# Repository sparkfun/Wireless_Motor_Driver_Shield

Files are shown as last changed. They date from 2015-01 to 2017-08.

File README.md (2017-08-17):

SparkFun Wireless Motor Driver Shield
=====================================

SparkFun Wireless Motor Driver Shield

[*SparkFun Wireless Motor Driver Shield (DEV-14285)*](https://www.sparkfun.com/products/14285)
Arduino shield with built-in motor driver and XBee slot.

This is an Arduino shield that integrates an H-Bridge Driver and breaks out 
all I/O ports to three-pin headers on a GND / PWR / SIG standard. This enables quick
prototyping and integration of Arduino projects without the need of a breadboard.

This board contains an XBee header for adding wireless capability to your Arduino projects. A switch for 
SW_Serial ties the TX/RX lines to pins A0 and A1 on the Arduino board. 

This shield is a perfect addition to building up a simiple robotics platform with an
Arduino board. Two switches allow you to select which power source is used to power the motors and/or servos.
See [the hookup guide](https://learn.sparkfun.com/tutorials/wireless-motor-driver-shield-hookup-guide#hardware-overview) for a chart showing the various switch configurations.

**Note:** If connected to your Arduino, the switch must be set to SW_Serial in order to program your board. 

Repository Contents
-------------------

* **/Firmware** - Example code 
* **/Hardware** - Eagle design files (.brd, .sch)
* **/Production** - Production panel files (.brd)

Documentation
--------------
* **[Hookup Guide](https://learn.sparkfun.com/tutorials/wireless-motor-driver-shield-hookup-guide)** - Basic hookup guide for the Wireless Motor Driver Shield.
* **[SparkFun Fritzing repo](https://github.com/sparkfun/Fritzing_Parts)** - Fritzing diagrams for SparkFun products.
* **[SparkFun 3D Model repo](https://github.com/sparkfun/3D_Models)** - 3D models of SparkFun products. 

Version History
---------------
* [vH14](https://github.com/sparkfun/Ludus_ProtoShield_Wireless/tree/vH14) - Current version
* [vH11](https://github.com/sparkfun/Ludus_ProtoShield_Wireless/tree/V_1.1) - The product formerly known as the Ludus ProtoShield Wireless

License Information
-------------------

This product is _**open source**_! 

Please review the LICENSE.md file for license information. 

If you have any questions or concerns on licensing, please contact techsupport@sparkfun.com.

Distributed as-is; no warranty is given.

- Your friends at SparkFun.

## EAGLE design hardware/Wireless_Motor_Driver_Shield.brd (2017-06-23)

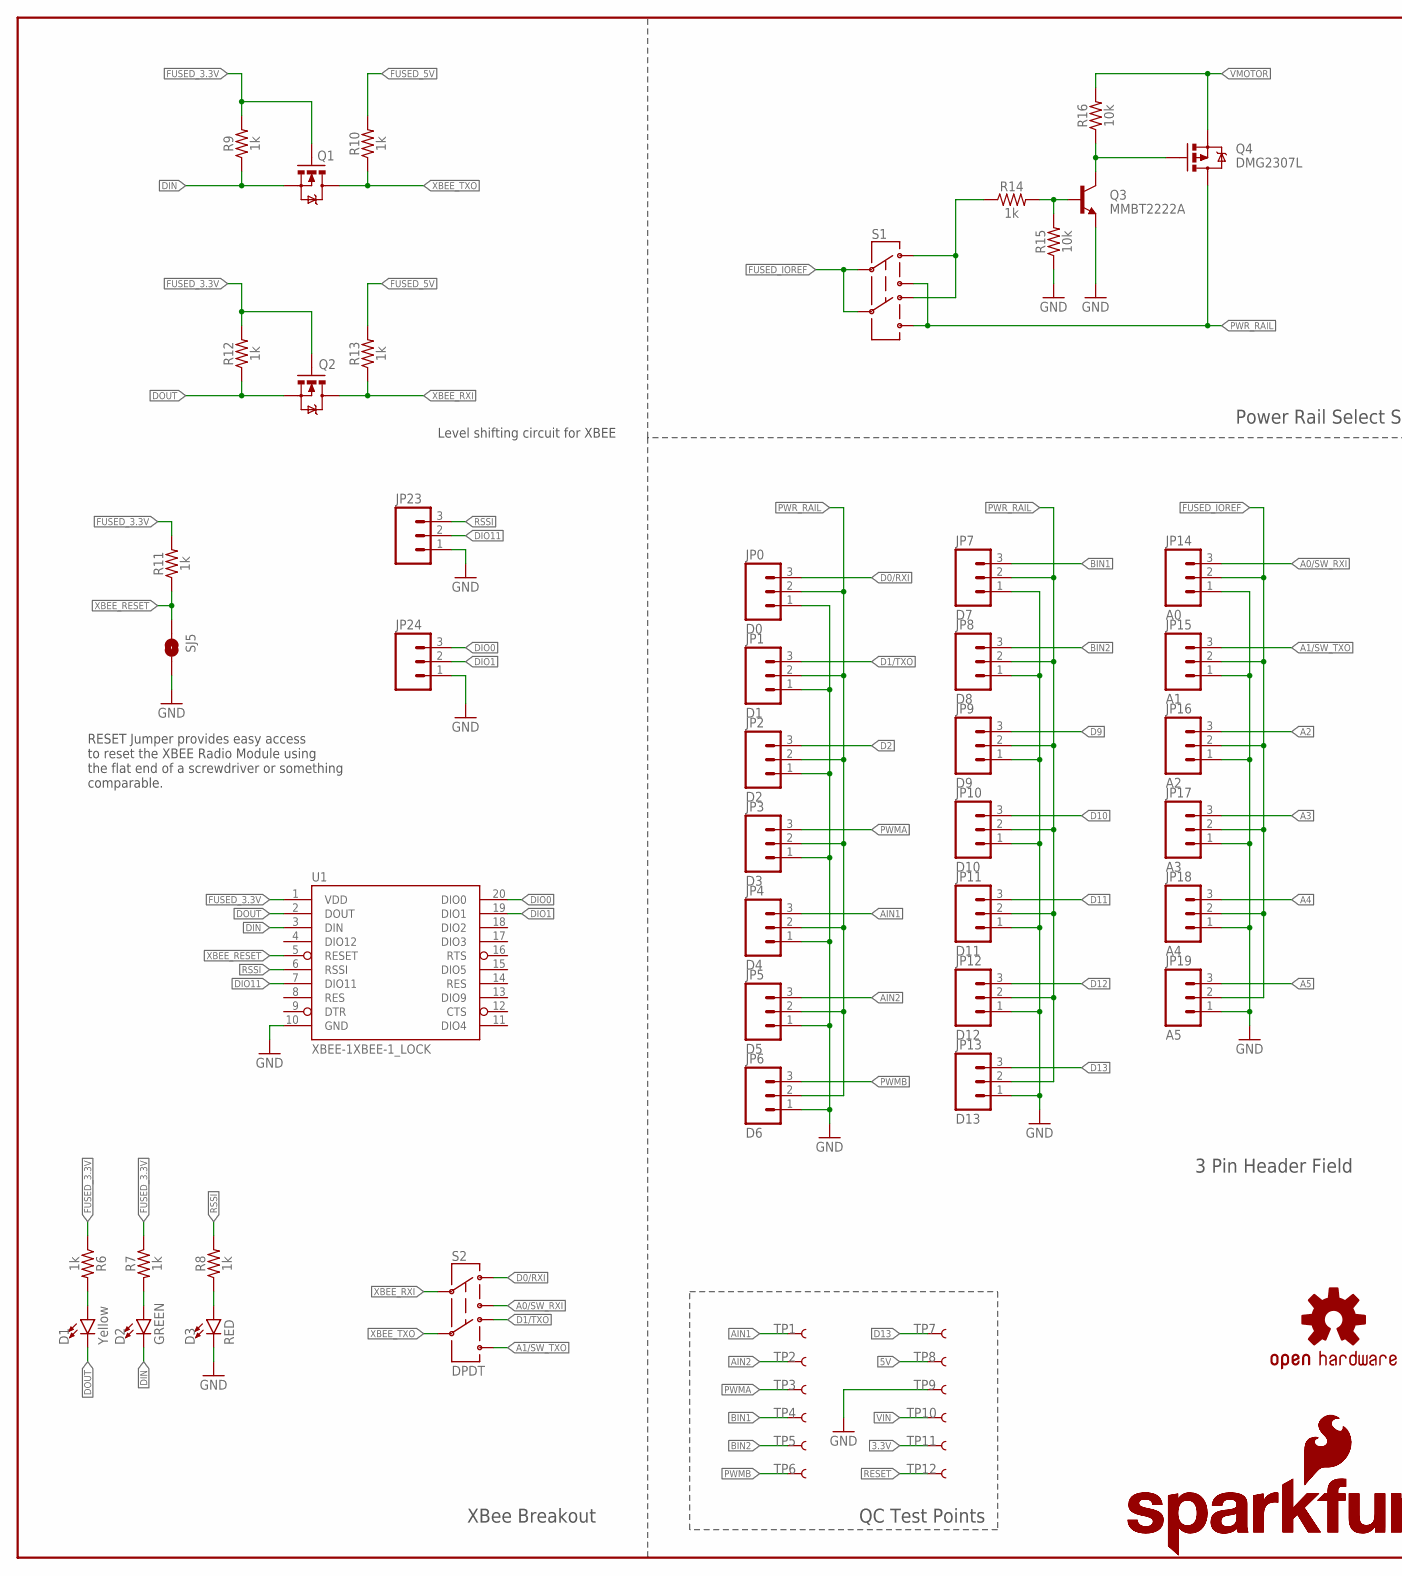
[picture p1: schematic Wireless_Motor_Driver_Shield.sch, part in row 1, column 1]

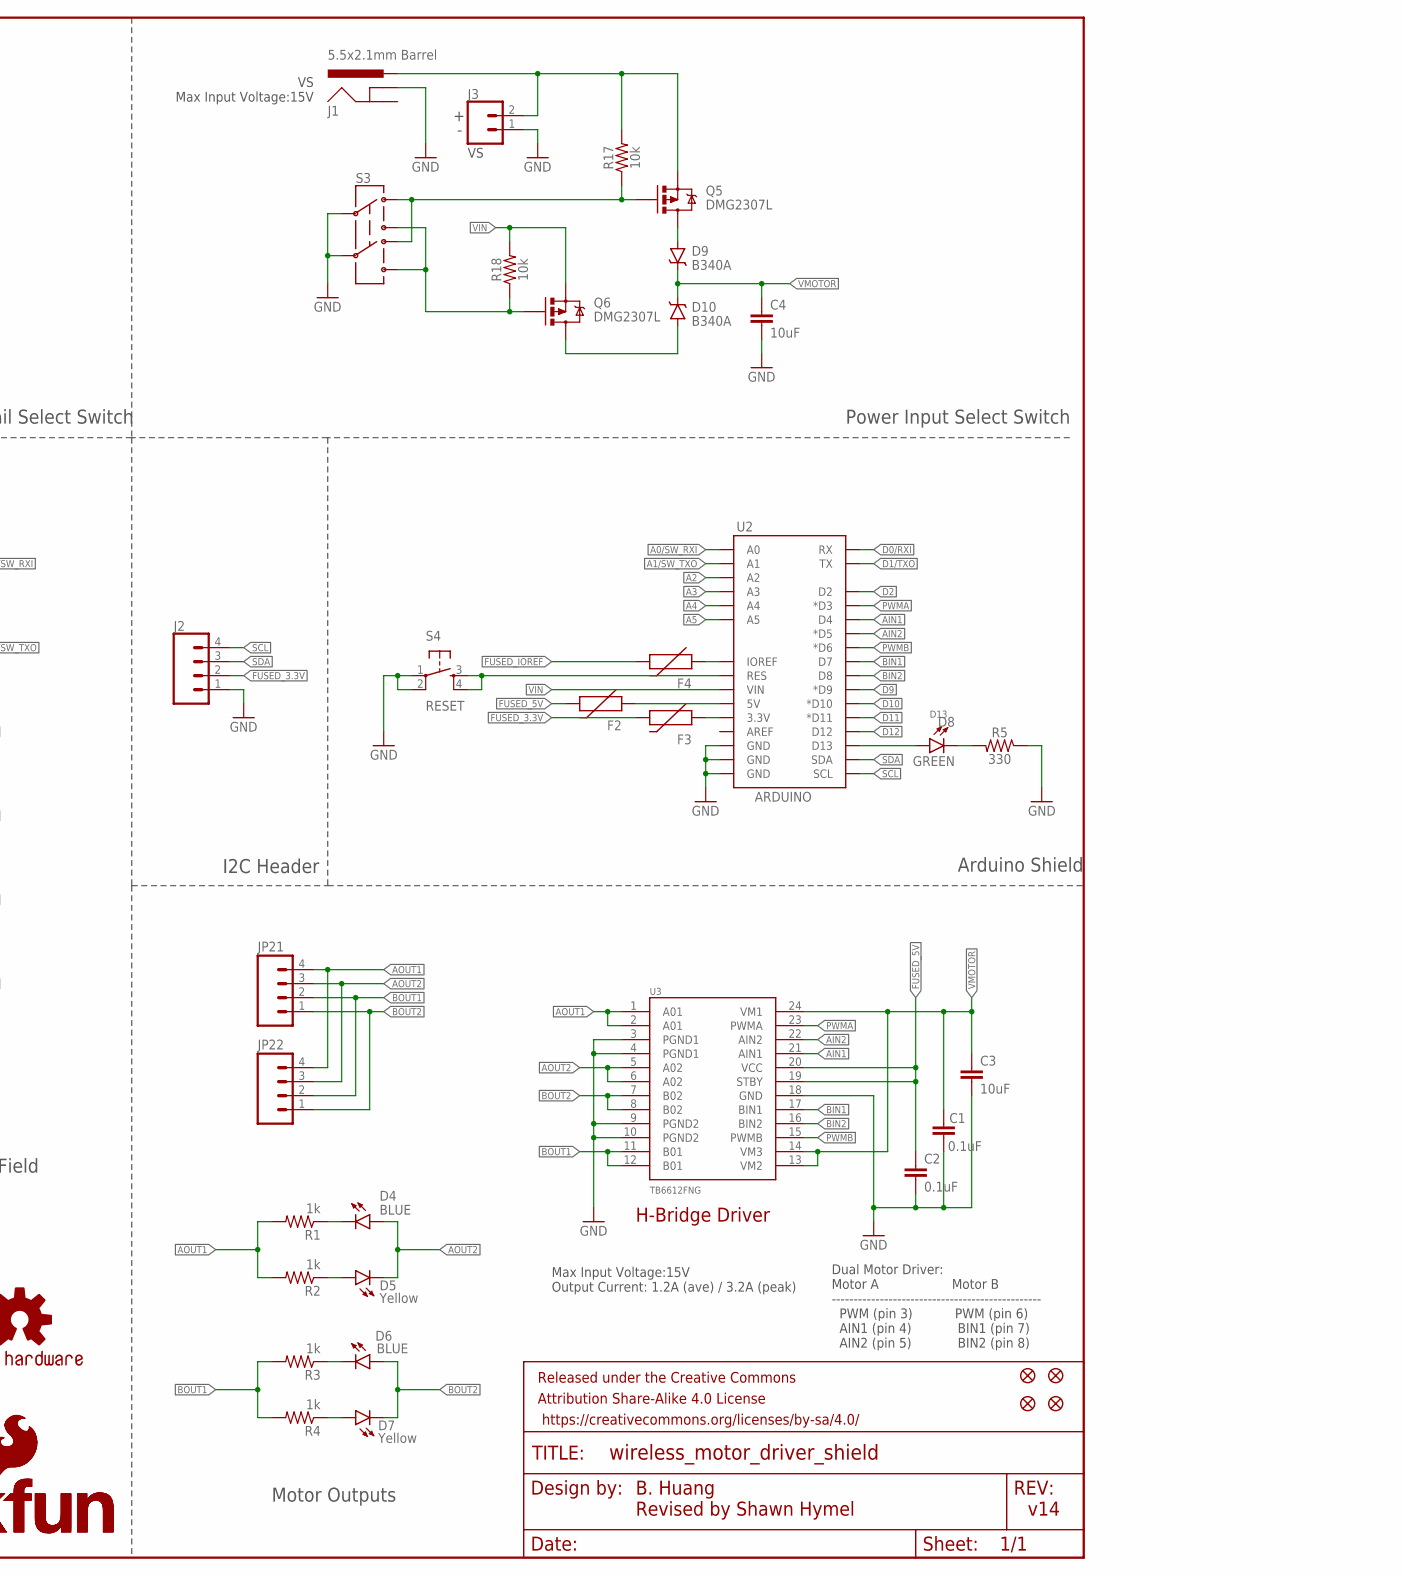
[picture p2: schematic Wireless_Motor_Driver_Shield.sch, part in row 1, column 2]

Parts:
C1, C2: 0.1uF; 0603
C3, C4: 10uF; 1210
D1, D5, D7: Yellow; LED-0603
D2, D8: GREEN; LED-0603
D3: RED; LED-0603
D4, D6: BLUE; LED-0603
D9, D10: B340A; SMA-DIODE
F2, F3, F4: PTCSMD; PTC-1206
FID1, FID2, FID3, FID4: FIDUCIAL1X2; FIDUCIAL-1X2
FRAME1: FRAME-LEDGER; CREATIVE_COMMONS
J1: 5.5x2.1mm Barrel; POWER_JACK_SMD
J2: CONN_04SMD_RA_FEMALE; 1X04_SMD_RA_FEMALE
J3: CONN_021X02_NO_SILK; 1X02_NO_SILK
JP0: D0; 1X03_LOCK
JP1: D1; 1X03_LOCK
JP2: D2; 1X03_LOCK
JP3: D3; 1X03_LOCK
JP4: D4; 1X03_LOCK
JP5: D5; 1X03_LOCK
JP6: D6; 1X03_LOCK
JP7: D7; 1X03_LOCK
JP8: D8; 1X03_LOCK
JP9: D9; 1X03_LOCK
JP10: D10; 1X03_LOCK
JP11: D11; 1X03_LOCK
JP12: D12; 1X03_LOCK
JP13: D13; 1X03_LOCK
JP14: A0; 1X03_LOCK
JP15: A1; 1X03_LOCK
JP16: A2; 1X03_LOCK
JP17: A3; 1X03_LOCK
JP18: A4; 1X03_LOCK
JP19: A5; 1X03_LOCK
JP21: M04PTH; 1X04@1
JP22: M04LOCK; 1X04_LOCK@1
JP23, JP24: M031X03_NO_SILK; 1X03_NO_SILK
LOGO1: OSHW-LOGOM; OSHW-LOGO-M
LOGO2, LOGO4: SFE_LOGO_NAME_FLAME.1_INCH; SFE_LOGO_NAME_FLAME_.1
LOGO3: SFE_LOGO_FLAME.2_INCH; SFE_LOGO_FLAME_.2
Q1, Q2: MOSFET-NCHANNELBSS138; SOT23-3
Q3: MMBT2222A; SOT23-3
Q4, Q5, Q6: DMG2307L; SOT23-3
R1, R2, R3, R4, R6, R7, R8, R9, R10, R11, R12, R13, R14: 1k; 0603
R5: 330; 0603
R15, R16, R17, R18: 10k; 0603
S1, S3: SWITCH-DPDTAYZ0202; AYZ0202
S2: DPDT; AYZ0202
S4: RESET; TACTILE-SWITCH-SMD
SJ5: SOLDERJUMPERNO; SJ_2S-NO
TP1, TP2, TP3, TP4, TP5, TP6, TP7, TP8, TP9, TP10, TP11, TP12: TEST-POINT3X5; PAD.03X.05
U1: XBEE-1XBEE-1_LOCK; XBEE-1_LOCK
U2: ARDUINO; UNO_R3_SHIELD_NOLABELS_LOCK
U3: TB6612FNG; SSOP24

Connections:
3.3V: F3.1, TP11.P$1, U2.3.3V
5V: F2.1, TP8.P$1, U2.5V
A0/SW_RXI: JP14.3, S2.3, U2.A0
A1/SW_TXO: JP15.3, S2.6, U2.A1
A2: JP16.3, U2.A2
A3: JP17.3, U2.A3
A4: JP18.3, U2.A4
A5: JP19.3, U2.A5
AIN1: JP4.3, TP1.P$1, U2.D4, U3.21 (AIN1)
AIN2: JP5.3, TP2.P$1, U2.D5 (*D5), U3.22 (AIN2)
AOUT1: JP21.4, JP22.4, R1.2, R2.2, U3.1 (A01), U3.2 (A01)
AOUT2: D4.A, D5.C, JP21.3, JP22.3, U3.5 (A02), U3.6 (A02)
BIN1: JP7.3, TP4.P$1, U2.D7, U3.17 (BIN1)
BIN2: JP8.3, TP5.P$1, U2.D8, U3.16 (BIN2)
BOUT1: JP21.2, JP22.2, R3.2, R4.2, U3.11 (B01), U3.12 (B01)
BOUT2: D6.A, D7.C, JP21.1, JP22.1, U3.7 (B02), U3.8 (B02)
D0/RXI: JP0.3, S2.1, U2.RX
D1/TXO: JP1.3, S2.4, U2.TX
D2: JP2.3, U2.D2
D9: JP9.3, U2.D9 (*D9)
D10: JP10.3, U2.D10 (*D10)
D11: JP11.3, U2.D11 (*D11)
D12: JP12.3, U2.D12
D13: D8.A, JP13.3, TP7.P$1, U2.D13
DIN: D2.C, Q1.2 (S), R9.1, U1.3 (DIN)
DIO0: JP24.3, U1.20 (DIO0)
DIO1: JP24.2, U1.19 (DIO1)
DIO11: JP23.2, U1.7 (DIO11)
DOUT: D1.C, Q2.2 (S), R12.1, U1.2 (DOUT)
FUSED_3.3V: F3.2, J2.2, Q1.1 (G), Q2.1 (G), R6.1, R7.1, R9.2, R11.2, R12.2, U1.1 (VDD)
FUSED_5V: C2.1, F2.2, R10.2, R13.2, U3.19 (STBY), U3.20 (VCC)
FUSED_IOREF: F4.2, JP14.2, JP15.2, JP16.2, JP17.2, JP18.2, JP19.2, S1.2, S1.5
GND: C1.2, C2.2, C3.2, C4.2, D3.C, J1.GND (GNDBREAK), J2.1, J3.1, JP0.1, JP1.1, JP2.1, JP3.1, JP4.1, JP5.1, JP6.1, JP7.1, JP8.1, JP9.1, JP10.1, JP11.1, JP12.1, JP13.1, JP14.1, JP15.1, JP16.1, JP17.1, JP18.1, JP19.1, JP23.1, JP24.1, Q3.2 (E), R5.1, R15.1, S3.2, S3.5, S4.1, S4.2, SJ5.2, TP9.P$1, U1.10 (GND), U2.GND@0 (GND), U2.GND@1 (GND), U2.GND@2 (GND), U3.3 (PGND1), U3.4 (PGND1), U3.9 (PGND2), U3.10 (PGND2), U3.18 (GND)
IOREF: F4.1, U2.IOREF
unnamed: D8.C, R5.2
unnamed: Q3.1 (B), R14.2, R15.2
unnamed: D5.A, R2.1
unnamed: Q6.1 (G), R18.1, S3.3, S3.6
unnamed: D4.C, R1.1
unnamed: D7.A, R4.1
unnamed: D6.C, R3.1
unnamed: J1.VIN0 (PWR), J3.2, Q5.2 (S), R17.2
unnamed: Q3.3 (C), Q4.1 (G), R16.1
unnamed: Q5.1 (G), R17.1, S3.1, S3.4
unnamed: R14.1, S1.1, S1.4
unnamed: D9.A, Q5.3 (D)
unnamed: D10.A, Q6.3 (D)
unnamed: D1.A, R6.2
unnamed: D2.A, R7.2
unnamed: D3.A, R8.1
PWMA: JP3.3, TP3.P$1, U2.D3 (*D3), U3.23 (PWMA)
PWMB: JP6.3, TP6.P$1, U2.D6 (*D6), U3.15 (PWMB)
PWR_RAIL: JP0.2, JP1.2, JP2.2, JP3.2, JP4.2, JP5.2, JP6.2, JP7.2, JP8.2, JP9.2, JP10.2, JP11.2, JP12.2, JP13.2, Q4.3 (D), S1.3, S1.6
RESET: S4.3, S4.4, TP12.P$1, U2.RES
RSSI: JP23.3, R8.2, U1.6 (RSSI)
SCL: J2.4, U2.SCL
SDA: J2.3, U2.SDA
VIN: Q6.2 (S), R18.2, TP10.P$1, U2.VIN
VMOTOR: C1.1, C3.1, C4.1, D9.C, D10.C, Q4.2 (S), R16.2, U3.13 (VM2), U3.14 (VM3), U3.24 (VM1)
XBEE_RESET: R11.1, SJ5.1, U1.5 (RESET)
XBEE_RXI: Q2.3 (D), R13.1, S2.2
XBEE_TXO: Q1.3 (D), R10.1, S2.5

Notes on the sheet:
Arduino Shield
H-Bridge Driver
Motor Outputs
B. Huang Revised by Shawn Hymel
v14
I2C Header
3 Pin Header Field
XBee Breakout
Power Rail Select Switch
Max Input Voltage:15V Output Current: 1.2A (ave) / 3.2A (peak)
RESET Jumper provides easy access to reset the XBEE Radio Module using the flat end of a screwdriver or something comparable.
Level shifting circuit for XBEE
QC Test Points
Dual Motor Driver: Motor A Motor B ------------------------------------------------ PWM (pin 3) PWM (pin 6) AIN1 (pin 4) BIN1 (pin 7) AIN2 (pin 5) BIN2 (pin 8)
Power Input Select Switch
VS Max Input Voltage:15V

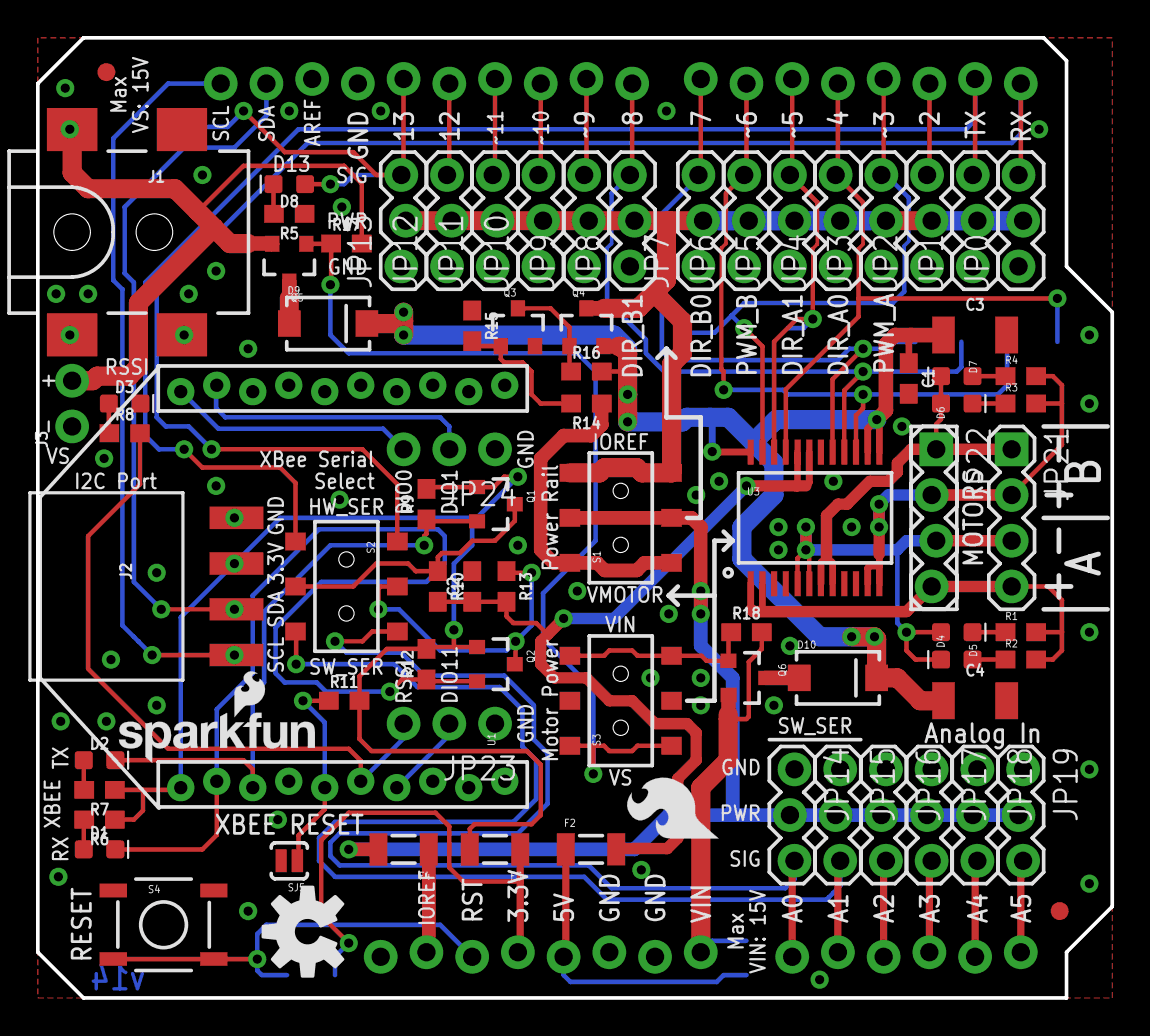
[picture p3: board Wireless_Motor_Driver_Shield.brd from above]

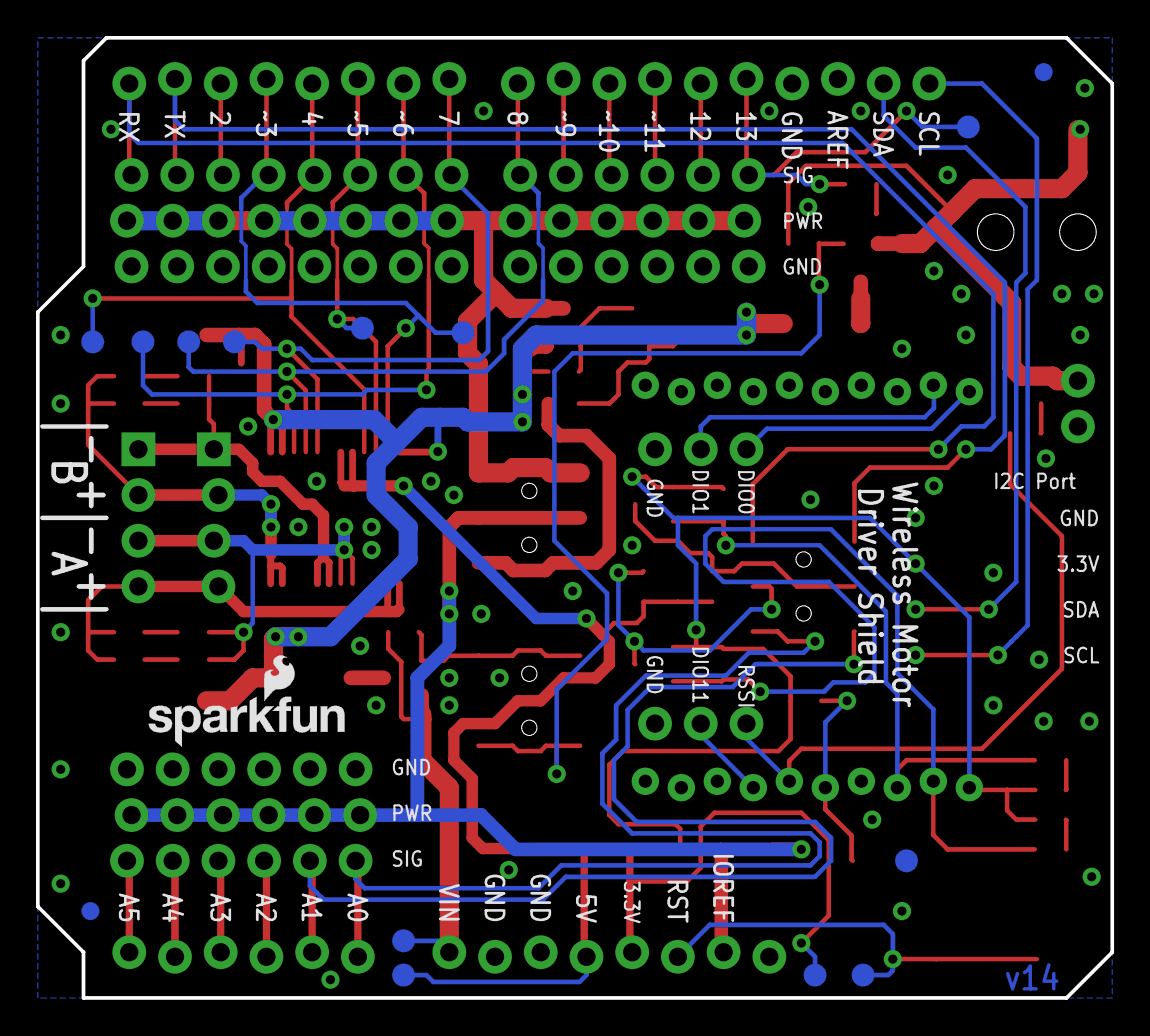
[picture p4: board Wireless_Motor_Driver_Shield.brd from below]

Board: 2 copper layers, 59.7 x 53.3 mm, 97 parts (15 on the bottom side), 62 nets.

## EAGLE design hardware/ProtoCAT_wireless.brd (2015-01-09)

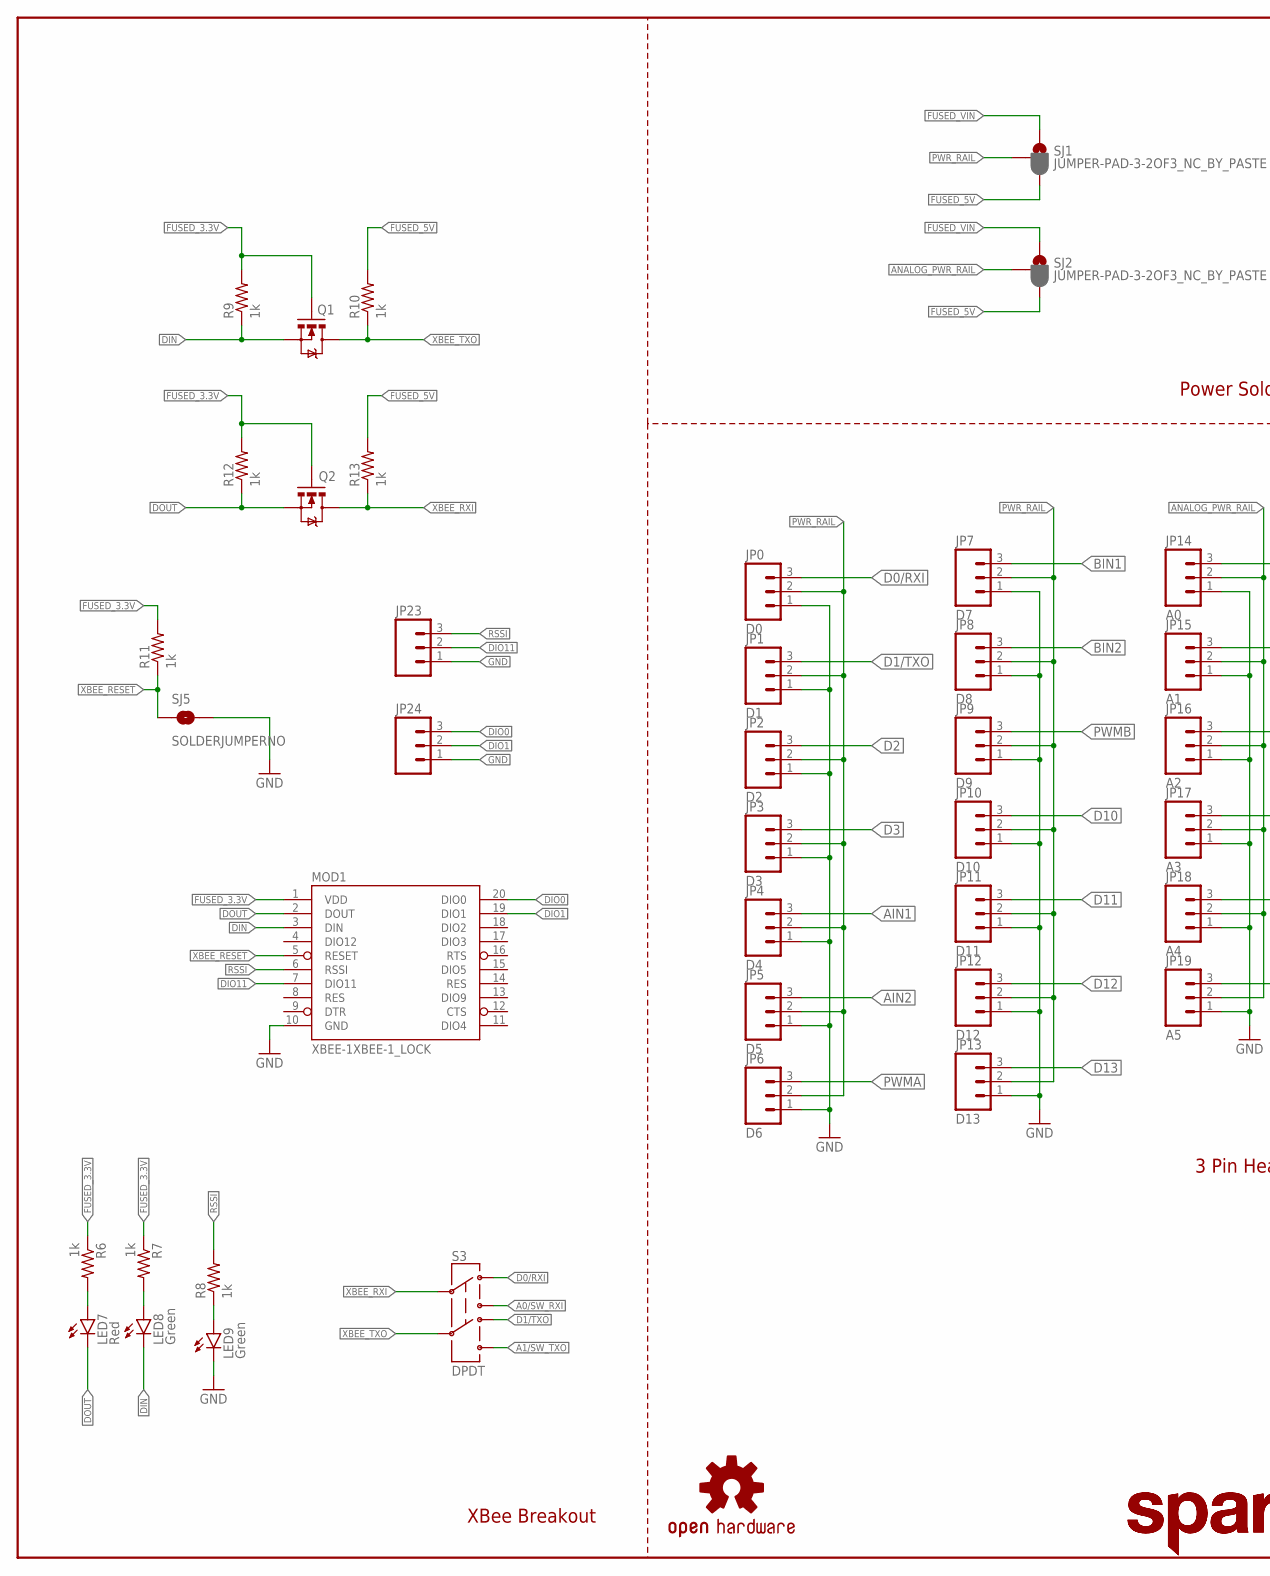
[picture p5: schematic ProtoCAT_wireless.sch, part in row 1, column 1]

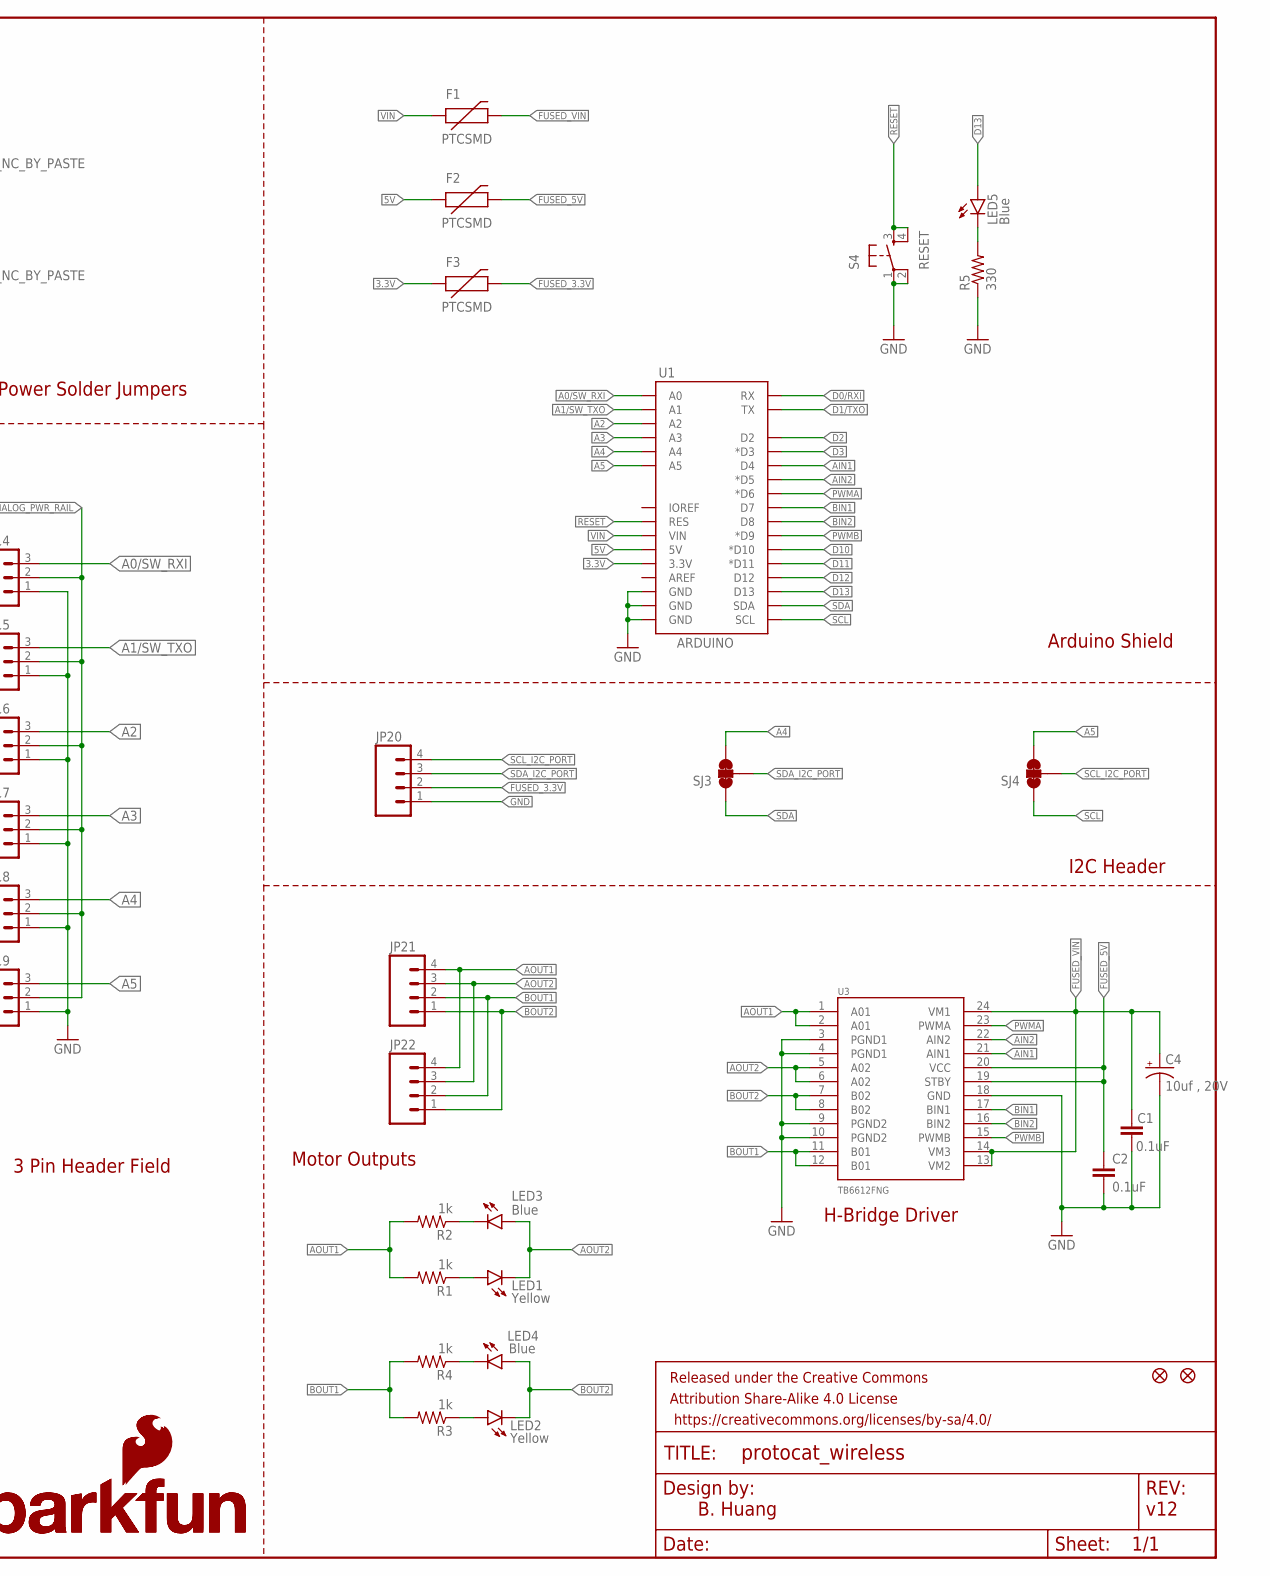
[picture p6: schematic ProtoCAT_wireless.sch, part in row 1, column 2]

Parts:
C1, C2: 0.1uF; 0603-CAP
C4: 10uf , 20V; EIA3528
F1, F2, F3: PTCSMD; PTC-1206
FID1, FID2: FIDUCIAL1X2; FIDUCIAL-1X2
FRAME1: FRAME-LEDGER; CREATIVE_COMMONS
JP0: D0; 1X03_LOCK
JP1: D1; 1X03_LOCK
JP2: D2; 1X03_LOCK
JP3: D3; 1X03_LOCK
JP4: D4; 1X03_LOCK
JP5: D5; 1X03_LOCK
JP6: D6; 1X03_LOCK
JP7: D7; 1X03_LOCK
JP8: D8; 1X03_LOCK
JP9: D9; 1X03_LOCK
JP10: D10; 1X03_LOCK
JP11: D11; 1X03_LOCK
JP12: D12; 1X03_LOCK
JP13: D13; 1X03_LOCK
JP14: A0; 1X03_LOCK
JP15: A1; 1X03_LOCK
JP16: A2; 1X03_LOCK
JP17: A3; 1X03_LOCK
JP18: A4; 1X03_LOCK
JP19: A5; 1X03_LOCK
JP20, JP21: M04PTH; 1X04
JP22: M04SMD_STRAIGHT_COMBO; 1X04_SMD_STRAIGHT_COMBO
JP23, JP24: M031X03_NO_SILK; 1X03_NO_SILK
LED1, LED2: Yellow; LED-0603
LED3, LED4, LED5: Blue; LED-0603
LED7: Red; LED-0603
LED8, LED9: Green; LED-0603
LOGO1: OSHW-LOGOM; OSHW-LOGO-M
LOGO2, LOGO4: SFE_LOGO_NAME_FLAME.1_INCH; SFE_LOGO_NAME_FLAME_.1
LOGO3: SFE_LOGO_FLAME.2COP; SFE_LOGO_FLAME_COPPER_.2
MOD1: XBEE-1XBEE-1_LOCK; XBEE-1_LOCK
Q1, Q2: MOSFET-NCHANNELSMD; SOT23-3
R1, R2, R3, R4, R6, R7, R8, R9, R10, R11, R12, R13: 1k; 0603-RES
R5: 330; 0603-RES
S3: DPDT; AYZ0202
S4: RESET; TACTILE-SWITCH-SMD
SJ1, SJ2: JUMPER-PAD-3-2OF3_NC_BY_PASTE; PAD-JUMPER-3-2OF3_NC_BY_PASTE_YES_SILK_FULL_BOX
SJ3, SJ4: JUMPER-PAD-3-NC_BY_TRACE; PAD-JUMPER-3-3OF3_NC_BY_TRACE_YES_SILK_FULL_BOX
SJ5: SOLDERJUMPERNO; SJ_2S-NO
U1: ARDUINO; UNO_R3_SHIELD_NOLABELS
U3: TB6612FNG; SSOP24
U$1: SFE_LUDUS; SFE_LUDUS-M

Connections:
3.3V: F3.1, U1.3.3V
5V: F2.1, U1.5V
A0/SW_RXI: JP14.3, S3.3, U1.A0
A1/SW_TXO: JP15.3, S3.6, U1.A1
A2: JP16.3, U1.A2
A3: JP17.3, U1.A3
A4: JP18.3, SJ3.3, U1.A4
A5: JP19.3, SJ4.3, U1.A5
AIN1: JP4.3, U1.D4, U3.21 (AIN1)
AIN2: JP5.3, U1.D5 (*D5), U3.22 (AIN2)
ANALOG_PWR_RAIL: JP14.2, JP15.2, JP16.2, JP17.2, JP18.2, JP19.2, SJ2.2
AOUT1: JP21.4, JP22.4, R1.2, R2.2, U3.1 (A01), U3.2 (A01)
AOUT2: JP21.3, JP22.3, LED1.C, LED3.A, U3.5 (A02), U3.6 (A02)
BIN1: JP7.3, U1.D7, U3.17 (BIN1)
BIN2: JP8.3, U1.D8, U3.16 (BIN2)
BOUT1: JP21.2, JP22.2, R3.2, R4.2, U3.11 (B01), U3.12 (B01)
BOUT2: JP21.1, JP22.1, LED2.C, LED4.A, U3.7 (B02), U3.8 (B02)
D0/RXI: JP0.3, S3.1, U1.RX
D1/TXO: JP1.3, S3.4, U1.TX
D2: JP2.3, U1.D2
D3: JP3.3, U1.D3 (*D3)
D10: JP10.3, U1.D10 (*D10)
D11: JP11.3, U1.D11 (*D11)
D12: JP12.3, U1.D12
D13: JP13.3, LED5.A, U1.D13
DIN: LED8.C, MOD1.3 (DIN), Q1.2 (S), R9.1
DIO0: JP24.3, MOD1.20 (DIO0)
DIO1: JP24.2, MOD1.19 (DIO1)
DIO11: JP23.2, MOD1.7 (DIO11)
DOUT: LED7.C, MOD1.2 (DOUT), Q2.2 (S), R12.1
FUSED_3.3V: F3.2, JP20.2, MOD1.1 (VDD), Q1.1 (G), Q2.1 (G), R6.1, R7.1, R9.2, R11.2, R12.2
FUSED_5V: C2.1, F2.2, R10.2, R13.2, SJ1.3, SJ2.3, U3.19 (STBY), U3.20 (VCC)
FUSED_VIN: C1.1, C4.A (+), F1.2, SJ1.1, SJ2.1, U3.13 (VM2), U3.14 (VM3), U3.24 (VM1)
GND: C1.2, C2.2, C4.C (-), JP0.1, JP1.1, JP2.1, JP3.1, JP4.1, JP5.1, JP6.1, JP7.1, JP8.1, JP9.1, JP10.1, JP11.1, JP12.1, JP13.1, JP14.1, JP15.1, JP16.1, JP17.1, JP18.1, JP19.1, JP20.1, JP23.1, JP24.1, LED9.C, MOD1.10 (GND), R5.1, S4.1, S4.2, SJ5.2, U1.GND@0 (GND), U1.GND@1 (GND), U1.GND@2 (GND), U3.3 (PGND1), U3.4 (PGND1), U3.9 (PGND2), U3.10 (PGND2), U3.18 (GND)
unnamed: LED5.C, R5.2
unnamed: LED1.A, R1.1
unnamed: LED3.C, R2.1
unnamed: LED2.A, R3.1
unnamed: LED4.C, R4.1
unnamed: LED7.A, R6.2
unnamed: LED8.A, R7.2
unnamed: LED9.A, R8.1
PWMA: JP6.3, U1.D6 (*D6), U3.23 (PWMA)
PWMB: JP9.3, U1.D9 (*D9), U3.15 (PWMB)
PWR_RAIL: JP0.2, JP1.2, JP2.2, JP3.2, JP4.2, JP5.2, JP6.2, JP7.2, JP8.2, JP9.2, JP10.2, JP11.2, JP12.2, JP13.2, SJ1.2
RESET: S4.3, S4.4, U1.RES
RSSI: JP23.3, MOD1.6 (RSSI), R8.2
SCL: SJ4.1, U1.SCL
SCL_I2C_PORT: JP20.4, SJ4.2
SDA: SJ3.1, U1.SDA
SDA_I2C_PORT: JP20.3, SJ3.2
VIN: F1.1, U1.VIN
XBEE_RESET: MOD1.5 (RESET), R11.1, SJ5.1
XBEE_RXI: Q2.3 (D), R13.1, S3.2
XBEE_TXO: Q1.3 (D), R10.1, S3.5

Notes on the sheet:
Arduino Shield
H-Bridge Driver
Motor Outputs
B. Huang
v12
I2C Header
3 Pin Header Field
XBee Breakout
Power Solder Jumpers

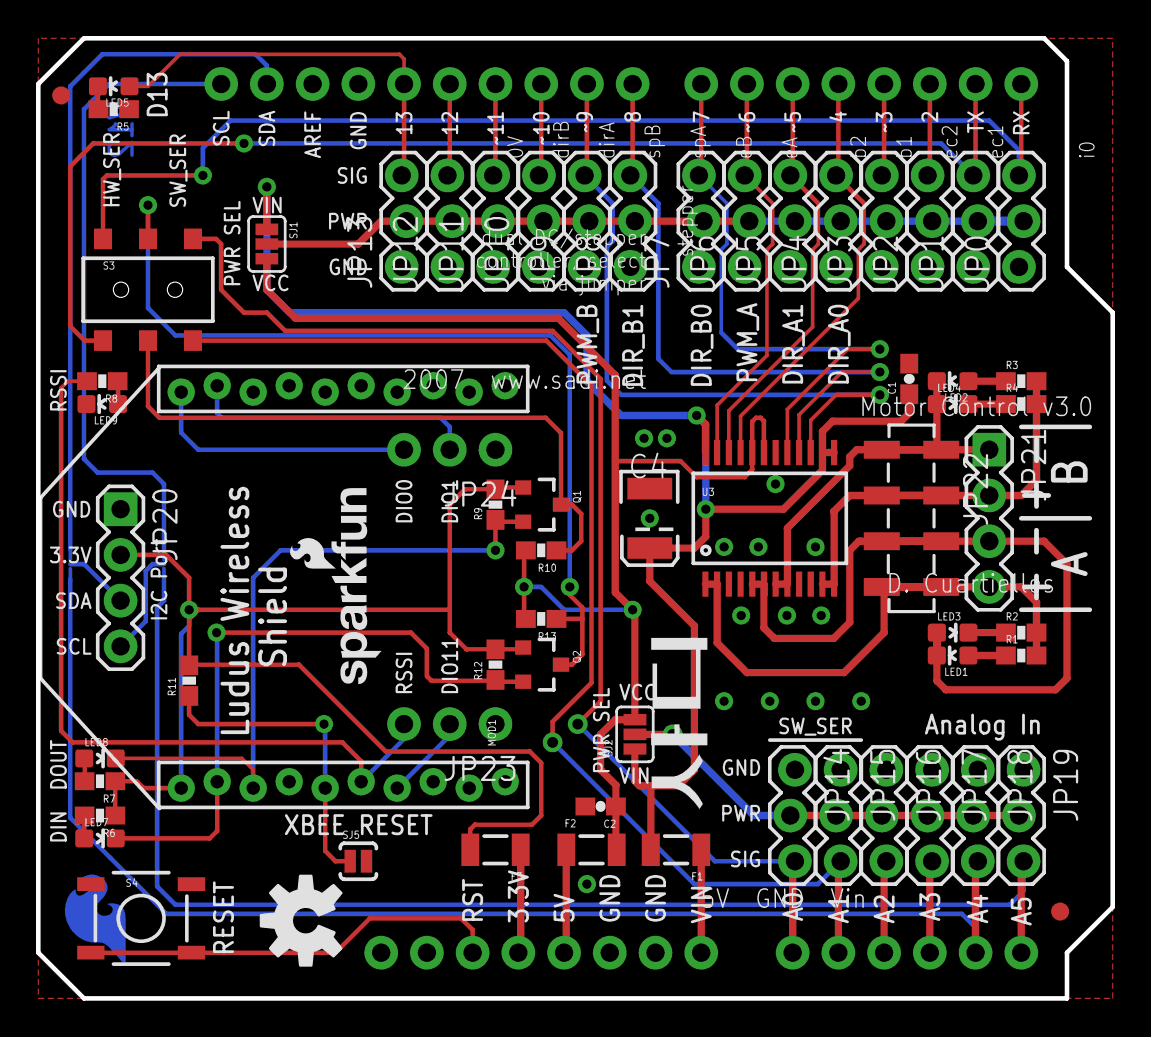
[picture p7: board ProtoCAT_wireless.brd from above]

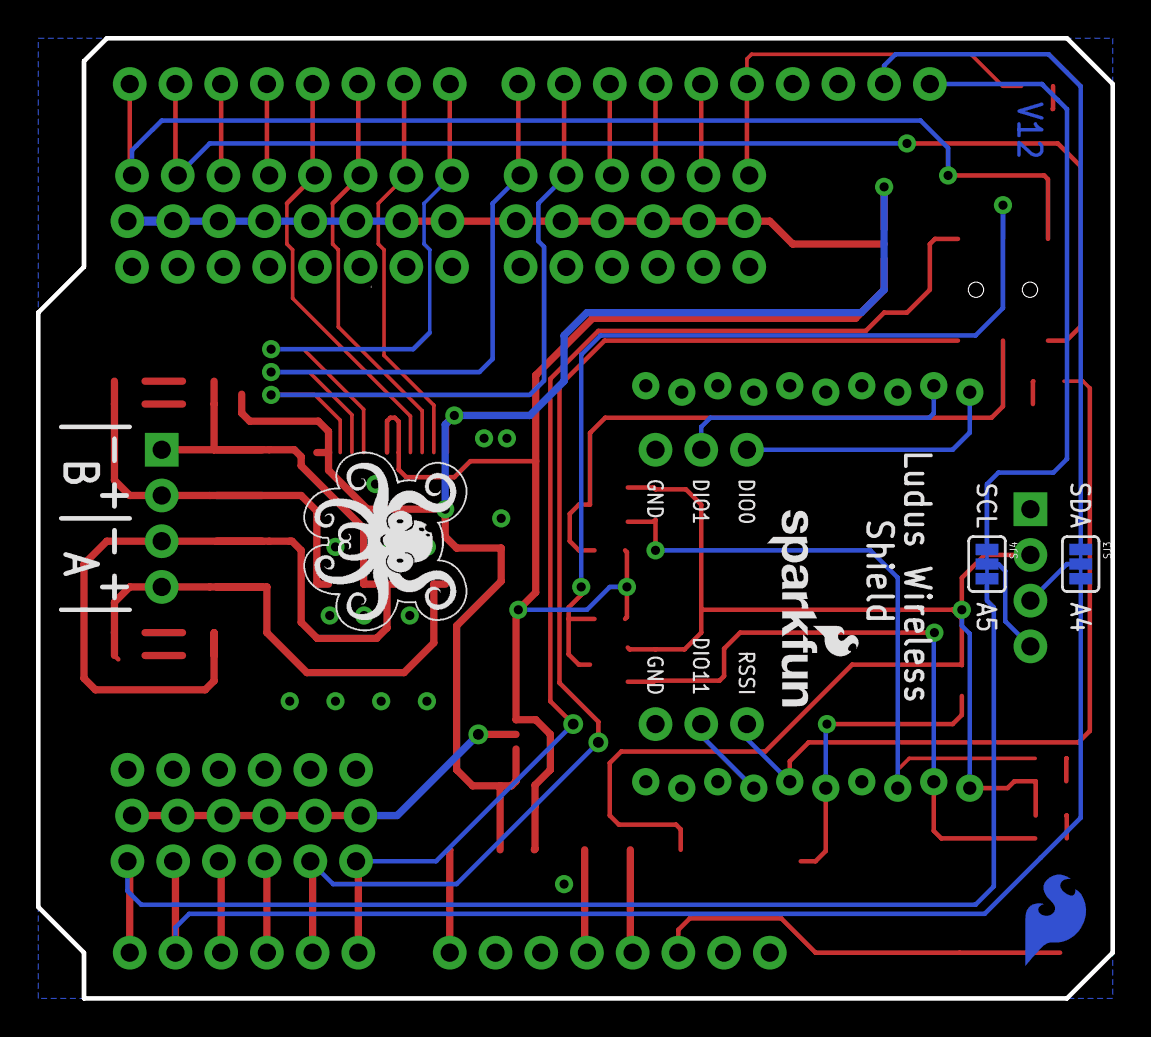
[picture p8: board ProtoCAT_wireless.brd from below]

Board: 2 copper layers, 59.7 x 53.3 mm, 72 parts (4 on the bottom side), 55 nets.

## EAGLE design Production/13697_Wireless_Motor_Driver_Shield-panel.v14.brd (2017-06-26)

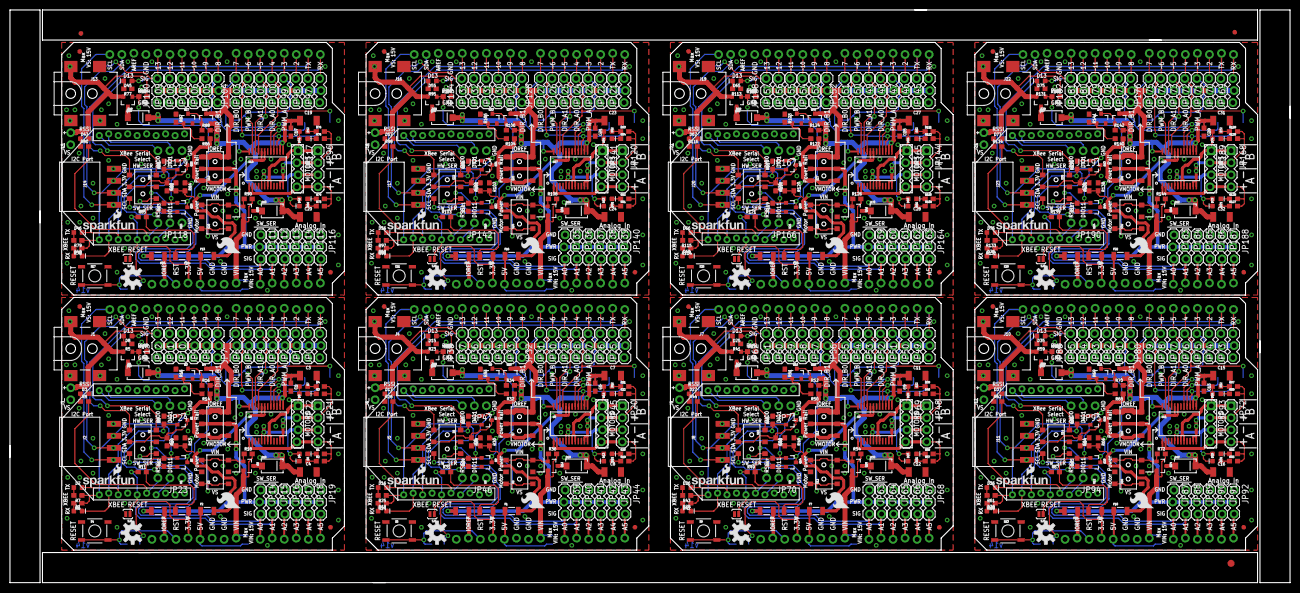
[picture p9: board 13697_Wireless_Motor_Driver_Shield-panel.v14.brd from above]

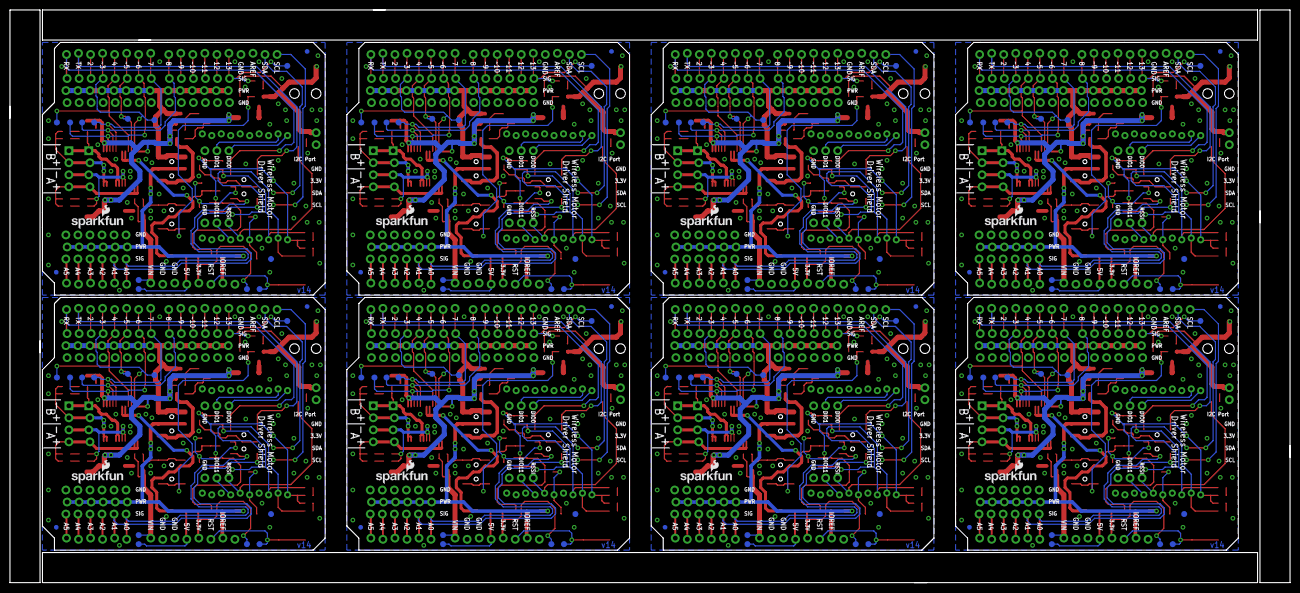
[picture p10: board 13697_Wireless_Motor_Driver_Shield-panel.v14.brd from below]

Board: 2 copper layers, 270.3 x 120.9 mm, 771 parts (120 on the bottom side), 496 nets.

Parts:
C1, C2, C5, C6, C9, C10, C13, C14, C17, C18, C21, C22, C25, C26, C29, C30: 0.1uF; 0603
C3, C4, C7, C8, C11, C12, C15, C16, C19, C20, C23, C24, C27, C28, C31, C32: 10uF; 1210
D1, D5, D7, D11, D12, D18, D21, D22, D28, D31, D32, D38, D41, D42, D48, D51, D52, D58, D61, D62, D68, D71, D72, D78: Yellow; LED-0603
D2, D8, D15, D16, D25, D26, D35, D36, D45, D46, D55, D56, D65, D66, D75, D76: GREEN; LED-0603
D3, D17, D27, D37, D47, D57, D67, D77: RED; LED-0603
D4, D6, D13, D14, D23, D24, D33, D34, D43, D44, D53, D54, D63, D64, D73, D74: BLUE; LED-0603
D9, D10, D19, D20, D29, D30, D39, D40, D49, D50, D59, D60, D69, D70, D79, D80: B340A; SMA-DIODE
E$1: FIDUCIAL-1.5X3
E$5, E$6: FIDUCIAL-1X2
F1, F2, F3, F4, F5, F6, F7, F8, F9, F10, F11, F12, F13, F14, F15, F16, F17, F18, F19, F20, F21, F22, F23, F24: PTC-1206
FID1, FID2, FID3, FID4, FID5, FID6, FID7, FID8, FID9, FID10, FID11, FID12, FID13, FID14, FID15, FID16, FID17, FID18, FID19, FID20, FID21, FID22, FID23, FID24, FID25, FID26, FID27, FID28, FID29, FID30, FID31, FID32: FIDUCIAL1X2; FIDUCIAL-1X2
J1, J4, J7, J10, J13, J16, J19, J22: 5.5x2.1mm Barrel; POWER_JACK_SMD
J2, J5, J8, J11, J14, J17, J20, J23: 1X04_SMD_RA_FEMALE
J3, J6, J9, J12, J15, J18, J21, J24: 1X02_NO_SILK
JP0, JP25, JP49, JP73, JP97, JP121, JP145, JP169: D0; 1X03_LOCK
JP1, JP26, JP50, JP74, JP98, JP122, JP146, JP170: D1; 1X03_LOCK
JP2, JP27, JP51, JP75, JP99, JP123, JP147, JP171: D2; 1X03_LOCK
JP3, JP28, JP52, JP76, JP100, JP124, JP148, JP172: D3; 1X03_LOCK
JP4, JP29, JP53, JP77, JP101, JP125, JP149, JP173: D4; 1X03_LOCK
JP5, JP30, JP54, JP78, JP102, JP126, JP150, JP174: D5; 1X03_LOCK
JP6, JP31, JP55, JP79, JP103, JP127, JP151, JP175: D6; 1X03_LOCK
JP7, JP32, JP56, JP80, JP104, JP128, JP152, JP176: D7; 1X03_LOCK
JP8, JP33, JP57, JP81, JP105, JP129, JP153, JP177: D8; 1X03_LOCK
JP9, JP34, JP58, JP82, JP106, JP130, JP154, JP178: D9; 1X03_LOCK
JP10, JP35, JP59, JP83, JP107, JP131, JP155, JP179: D10; 1X03_LOCK
JP11, JP36, JP60, JP84, JP108, JP132, JP156, JP180: D11; 1X03_LOCK
JP12, JP37, JP61, JP85, JP109, JP133, JP157, JP181: D12; 1X03_LOCK
JP13, JP38, JP62, JP86, JP110, JP134, JP158, JP182: D13; 1X03_LOCK
JP14, JP39, JP63, JP87, JP111, JP135, JP159, JP183: A0; 1X03_LOCK
JP15, JP40, JP64, JP88, JP112, JP136, JP160, JP184: A1; 1X03_LOCK
JP16, JP41, JP65, JP89, JP113, JP137, JP161, JP185: A2; 1X03_LOCK
JP17, JP42, JP66, JP90, JP114, JP138, JP162, JP186: A3; 1X03_LOCK
JP18, JP43, JP67, JP91, JP115, JP139, JP163, JP187: A4; 1X03_LOCK
JP19, JP44, JP68, JP92, JP116, JP140, JP164, JP188: A5; 1X03_LOCK
JP20, JP21, JP48, JP72, JP96, JP120, JP144, JP168: 1X04@1
JP22, JP45, JP69, JP93, JP117, JP141, JP165, JP189: 1X04_LOCK@1
JP23, JP24, JP46, JP47, JP70, JP71, JP94, JP95, JP118, JP119, JP142, JP143, JP166, JP167, JP190, JP191: 1X03_NO_SILK
LOGO1, LOGO5, LOGO9, LOGO13, LOGO17, LOGO21, LOGO25, LOGO29: OSHW-LOGOM; OSHW-LOGO-M
LOGO2, LOGO4, LOGO6, LOGO8, LOGO10, LOGO12, LOGO14, LOGO16, LOGO18, LOGO20, LOGO22, LOGO24, LOGO26, LOGO28, LOGO30, LOGO32: SFE_LOGO_NAME_FLAME.1_INCH; SFE_LOGO_NAME_FLAME_.1
LOGO3, LOGO7, LOGO11, LOGO15, LOGO19, LOGO23, LOGO27, LOGO31: SFE_LOGO_FLAME.2_INCH; SFE_LOGO_FLAME_.2
Q1, Q2, Q7, Q8, Q13, Q14, Q19, Q20, Q25, Q26, Q31, Q32, Q37, Q38, Q43, Q44: MOSFET-NCHANNELBSS138; SOT23-3
Q3, Q9, Q15, Q21, Q27, Q33, Q39, Q45: MMBT2222A; SOT23-3
Q4, Q5, Q6, Q10, Q11, Q12, Q16, Q17, Q18, Q22, Q23, Q24, Q28, Q29, Q30, Q34, Q35, Q36, Q40, Q41, Q42, Q46, Q47, Q48: DMG2307L; SOT23-3
R1, R2, R3, R4, R6, R7, R8, R9, R10, R11, R12, R13, R14, R19, R20, R21, R22, R24, R25, R26, R27, R28, R29, R30, R31, R32, R37, R38, R39, R40, R42, R43, R44, R45, R46, R47, R48, R49, R50, R55, R56, R57, R58, R60, R61, R62, R63, R64, R65, R66, R67, R68, R73, R74, R75, R76, R78, R79, R80, R81, R82, R83, R84, R85, R86, R91, R92, R93, R94, R96, R97, R98, R99, R100, R101, R102, R103, R104, R109, R110, R111, R112, R114, R115, R116, R117, R118, R119, R120, R121, R122, R127, R128, R129, R130, R132, R133, R134, R135, R136, R137, R138, R139, R140: 1k; 0603
R5, R23, R41, R59, R77, R95, R113, R131: 330; 0603
R15, R16, R17, R18, R33, R34, R35, R36, R51, R52, R53, R54, R69, R70, R71, R72, R87, R88, R89, R90, R105, R106, R107, R108, R123, R124, R125, R126, R141, R142, R143, R144: 10k; 0603
S1, S3, S7, S8, S11, S12, S15, S16, S19, S20, S23, S24, S27, S28, S31, S32: AYZ0202
S2, S6, S10, S14, S18, S22, S26, S30: DPDT; AYZ0202
S4, S5, S9, S13, S17, S21, S25, S29: RESET; TACTILE-SWITCH-SMD
SJ1, SJ2, SJ3, SJ4, SJ5, SJ6, SJ7, SJ8: SJ_2S-NO
TP1, TP2, TP3, TP4, TP5, TP6, TP7, TP8, TP9, TP10, TP11, TP12, TP13, TP14, TP15, TP16, TP17, TP18, TP19, TP20, TP21, TP22, TP23, TP24, TP25, TP26, TP27, TP28, TP29, TP30, TP31, TP32, TP33, TP34, TP35, TP36, TP37, TP38, TP39, TP40, TP41, TP42, TP43, TP44, TP45, TP46, TP47, TP48, TP49, TP50, TP51, TP52, TP53, TP54, TP55, TP56, TP57, TP58, TP59, TP60, TP61, TP62, TP63, TP64, TP65, TP66, TP67, TP68, TP69, TP70, TP71, TP72, TP73, TP74, TP75, TP76, TP77, TP78, TP79, TP80, TP81, TP82, TP83, TP84, TP85, TP86, TP87, TP88, TP89, TP90, TP91, TP92, TP93, TP94, TP95, TP96: PAD.03X.05
U1, U6, U9, U12, U15, U18, U21, U24: XBEE-1XBEE-1_LOCK; XBEE-1_LOCK
U2, U4, U7, U10, U13, U16, U19, U22: ARDUINO; UNO_R3_SHIELD_NOLABELS_LOCK
U3, U5, U8, U11, U14, U17, U20, U23: TB6612FNG; SSOP24

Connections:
3.3V: F3.1, TP11.P$1, U2.3.3V
3.3V1: F5.1, TP23.P$1, U4.3.3V
3.3V2: F8.1, TP35.P$1, U7.3.3V
3.3V3: F11.1, TP47.P$1, U10.3.3V
3.3V4: F14.1, TP59.P$1, U13.3.3V
3.3V5: F17.1, TP71.P$1, U16.3.3V
3.3V6: F20.1, TP83.P$1, U19.3.3V
3.3V7: F23.1, TP95.P$1, U22.3.3V
5V: F2.1, TP8.P$1, U2.5V
5V1: F1.1, TP20.P$1, U4.5V
5V2: F7.1, TP32.P$1, U7.5V
5V3: F10.1, TP44.P$1, U10.5V
5V4: F13.1, TP56.P$1, U13.5V
5V5: F16.1, TP68.P$1, U16.5V
5V6: F19.1, TP80.P$1, U19.5V
5V7: F22.1, TP92.P$1, U22.5V
A0/SW_RXI: JP14.3, S2.3, U2.A0
A0/SW_RXI1: JP39.3, S6.3, U4.A0
A0/SW_RXI2: JP63.3, S10.3, U7.A0
A0/SW_RXI3: JP87.3, S14.3, U10.A0
A0/SW_RXI4: JP111.3, S18.3, U13.A0
A0/SW_RXI5: JP135.3, S22.3, U16.A0
A0/SW_RXI6: JP159.3, S26.3, U19.A0
A0/SW_RXI7: JP183.3, S30.3, U22.A0
A1: JP44.3, U4.A5
A1/SW_TXO: JP15.3, S2.6, U2.A1
A1/SW_TXO1: JP40.3, S6.6, U4.A1
A1/SW_TXO2: JP64.3, S10.6, U7.A1
A1/SW_TXO3: JP88.3, S14.6, U10.A1
A1/SW_TXO4: JP112.3, S18.6, U13.A1
A1/SW_TXO5: JP136.3, S22.6, U16.A1
A1/SW_TXO6: JP160.3, S26.6, U19.A1
A1/SW_TXO7: JP184.3, S30.6, U22.A1
A2: JP16.3, U2.A2
A3: JP17.3, U2.A3
A4: JP18.3, U2.A4
A5: JP19.3, U2.A5
A6: JP43.3, U4.A4
A7: JP41.3, U4.A2
A8: JP42.3, U4.A3
A9: JP68.3, U7.A5
A10: JP67.3, U7.A4
A11: JP65.3, U7.A2
A12: JP66.3, U7.A3
A13: JP92.3, U10.A5
A14: JP91.3, U10.A4
A15: JP89.3, U10.A2
A16: JP90.3, U10.A3
A17: JP116.3, U13.A5
A18: JP115.3, U13.A4
A19: JP113.3, U13.A2
A20: JP114.3, U13.A3
A21: JP140.3, U16.A5
A22: JP139.3, U16.A4
A23: JP137.3, U16.A2
A24: JP138.3, U16.A3
A25: JP164.3, U19.A5
A26: JP163.3, U19.A4
A27: JP161.3, U19.A2
A28: JP162.3, U19.A3
A29: JP188.3, U22.A5
A30: JP187.3, U22.A4
A31: JP185.3, U22.A2
A32: JP186.3, U22.A3
AIN1: JP4.3, TP1.P$1, U2.D4, U3.21
AIN2: JP5.3, TP2.P$1, U2.D5, U3.22
AIN3: JP30.3, TP14.P$1, U4.D5, U5.22
AIN4: JP29.3, TP13.P$1, U4.D4, U5.21
AIN5: JP54.3, TP26.P$1, U7.D5, U8.22
AIN6: JP53.3, TP25.P$1, U7.D4, U8.21
AIN7: JP78.3, TP38.P$1, U10.D5, U11.22
AIN8: JP77.3, TP37.P$1, U10.D4, U11.21
AIN9: JP102.3, TP50.P$1, U13.D5, U14.22
AIN10: JP101.3, TP49.P$1, U13.D4, U14.21
AIN11: JP126.3, TP62.P$1, U16.D5, U17.22
AIN12: JP125.3, TP61.P$1, U16.D4, U17.21
AIN13: JP150.3, TP74.P$1, U19.D5, U20.22
AIN14: JP149.3, TP73.P$1, U19.D4, U20.21
AIN15: JP174.3, TP86.P$1, U22.D5, U23.22
AIN16: JP173.3, TP85.P$1, U22.D4, U23.21
AOUT1: JP21.4, JP22.4, R1.2, R2.2, U3.1, U3.2
AOUT2: D4.A, D5.C, JP21.3, JP22.3, U3.5, U3.6
AOUT3: JP20.4, JP45.4, R19.2, R20.2, U5.1, U5.2
AOUT4: D11.C, D13.A, JP20.3, JP45.3, U5.5, U5.6
AOUT5: JP48.4, JP69.4, R37.2, R38.2, U8.1, U8.2
AOUT6: D21.C, D23.A, JP48.3, JP69.3, U8.5, U8.6
AOUT7: JP72.4, JP93.4, R55.2, R56.2, U11.1, U11.2
AOUT8: D31.C, D33.A, JP72.3, JP93.3, U11.5, U11.6
AOUT9: JP96.4, JP117.4, R73.2, R74.2, U14.1, U14.2
AOUT10: D41.C, D43.A, JP96.3, JP117.3, U14.5, U14.6
AOUT11: JP120.4, JP141.4, R91.2, R92.2, U17.1, U17.2
AOUT12: D51.C, D53.A, JP120.3, JP141.3, U17.5, U17.6
AOUT13: JP144.4, JP165.4, R109.2, R110.2, U20.1, U20.2
AOUT14: D61.C, D63.A, JP144.3, JP165.3, U20.5, U20.6
AOUT15: JP168.4, JP189.4, R127.2, R128.2, U23.1, U23.2
AOUT16: D71.C, D73.A, JP168.3, JP189.3, U23.5, U23.6
BIN1: JP7.3, TP4.P$1, U2.D7, U3.17
BIN2: JP8.3, TP5.P$1, U2.D8, U3.16
BIN3: JP32.3, TP16.P$1, U4.D7, U5.17
BIN4: JP33.3, TP17.P$1, U4.D8, U5.16
BIN5: JP56.3, TP28.P$1, U7.D7, U8.17
BIN6: JP57.3, TP29.P$1, U7.D8, U8.16
BIN7: JP80.3, TP40.P$1, U10.D7, U11.17
BIN8: JP81.3, TP41.P$1, U10.D8, U11.16
BIN9: JP104.3, TP52.P$1, U13.D7, U14.17
BIN10: JP105.3, TP53.P$1, U13.D8, U14.16
BIN11: JP128.3, TP64.P$1, U16.D7, U17.17
BIN12: JP129.3, TP65.P$1, U16.D8, U17.16
BIN13: JP152.3, TP76.P$1, U19.D7, U20.17
BIN14: JP153.3, TP77.P$1, U19.D8, U20.16
BIN15: JP176.3, TP88.P$1, U22.D7, U23.17
BIN16: JP177.3, TP89.P$1, U22.D8, U23.16
BOUT1: JP21.2, JP22.2, R3.2, R4.2, U3.11, U3.12
BOUT2: D6.A, D7.C, JP21.1, JP22.1, U3.7, U3.8
BOUT3: D12.C, D14.A, JP20.1, JP45.1, U5.7, U5.8
BOUT4: JP20.2, JP45.2, R21.2, R22.2, U5.11, U5.12
BOUT5: D22.C, D24.A, JP48.1, JP69.1, U8.7, U8.8
BOUT6: JP48.2, JP69.2, R39.2, R40.2, U8.11, U8.12
BOUT7: D32.C, D34.A, JP72.1, JP93.1, U11.7, U11.8
BOUT8: JP72.2, JP93.2, R57.2, R58.2, U11.11, U11.12
BOUT9: D42.C, D44.A, JP96.1, JP117.1, U14.7, U14.8
BOUT10: JP96.2, JP117.2, R75.2, R76.2, U14.11, U14.12
BOUT11: D52.C, D54.A, JP120.1, JP141.1, U17.7, U17.8
BOUT12: JP120.2, JP141.2, R93.2, R94.2, U17.11, U17.12
BOUT13: D62.C, D64.A, JP144.1, JP165.1, U20.7, U20.8
BOUT14: JP144.2, JP165.2, R111.2, R112.2, U20.11, U20.12
BOUT15: D72.C, D74.A, JP168.1, JP189.1, U23.7, U23.8
BOUT16: JP168.2, JP189.2, R129.2, R130.2, U23.11, U23.12
D0/RXI: JP0.3, S2.1, U2.RX
D0/RXI1: JP25.3, S6.1, U4.RX
D0/RXI2: JP49.3, S10.1, U7.RX
D0/RXI3: JP73.3, S14.1, U10.RX
D0/RXI4: JP97.3, S18.1, U13.RX
D0/RXI5: JP121.3, S22.1, U16.RX
D0/RXI6: JP145.3, S26.1, U19.RX
D0/RXI7: JP169.3, S30.1, U22.RX
D1: JP37.3, U4.D12
D1/TXO: JP1.3, S2.4, U2.TX
D1/TXO1: JP26.3, S6.4, U4.TX
D1/TXO2: JP50.3, S10.4, U7.TX
D1/TXO3: JP74.3, S14.4, U10.TX
D1/TXO4: JP98.3, S18.4, U13.TX
D1/TXO5: JP122.3, S22.4, U16.TX
D1/TXO6: JP146.3, S26.4, U19.TX
D1/TXO7: JP170.3, S30.4, U22.TX
D2: JP2.3, U2.D2
D3: D15.A, JP38.3, TP19.P$1, U4.D13
D4: JP35.3, U4.D10
D5: JP27.3, U4.D2
D6: JP36.3, U4.D11
D7: JP34.3, U4.D9
D8: JP61.3, U7.D12
D9: JP9.3, U2.D9
D10: JP10.3, U2.D10
D11: JP11.3, U2.D11
D12: JP12.3, U2.D12
D13: D8.A, JP13.3, TP7.P$1, U2.D13
D14: D25.A, JP62.3, TP31.P$1, U7.D13
D15: JP59.3, U7.D10
D16: JP51.3, U7.D2
D17: JP60.3, U7.D11
D18: JP58.3, U7.D9
D19: JP85.3, U10.D12
D20: D35.A, JP86.3, TP43.P$1, U10.D13
D21: JP83.3, U10.D10
D22: JP75.3, U10.D2
D23: JP84.3, U10.D11
D24: JP82.3, U10.D9
D25: JP109.3, U13.D12
D26: D45.A, JP110.3, TP55.P$1, U13.D13
D27: JP107.3, U13.D10
D28: JP99.3, U13.D2
D29: JP108.3, U13.D11
D30: JP106.3, U13.D9
D31: JP133.3, U16.D12
D32: D55.A, JP134.3, TP67.P$1, U16.D13
D33: JP131.3, U16.D10
D34: JP123.3, U16.D2
D35: JP132.3, U16.D11
D36: JP130.3, U16.D9
D37: JP157.3, U19.D12
D38: D65.A, JP158.3, TP79.P$1, U19.D13
D39: JP155.3, U19.D10
D40: JP147.3, U19.D2
D41: JP156.3, U19.D11
D42: JP154.3, U19.D9
D43: JP181.3, U22.D12
D44: D75.A, JP182.3, TP91.P$1, U22.D13
D45: JP179.3, U22.D10
D46: JP171.3, U22.D2
D47: JP180.3, U22.D11
D48: JP178.3, U22.D9
DIN: D2.C, Q1.2, R9.1, U1.3
DIN1: D16.C, Q7.2, R27.1, U6.3
DIN2: D26.C, Q13.2, R45.1, U9.3
DIN3: D36.C, Q19.2, R63.1, U12.3
DIN4: D46.C, Q25.2, R81.1, U15.3
DIN5: D56.C, Q31.2, R99.1, U18.3
DIN6: D66.C, Q37.2, R117.1, U21.3
DIN7: D76.C, Q43.2, R135.1, U24.3
DIO0: JP24.3, U1.20
DIO1: JP24.2, U1.19
DIO2: JP46.2, U6.7
DIO3: JP47.3, U6.20
DIO4: JP47.2, U6.19
DIO5: JP70.2, U9.7
DIO6: JP71.3, U9.20
DIO7: JP71.2, U9.19
DIO8: JP94.2, U12.7
DIO9: JP95.3, U12.20
DIO10: JP95.2, U12.19
DIO11: JP23.2, U1.7
DIO12: JP118.2, U15.7
DIO13: JP119.3, U15.20
DIO14: JP119.2, U15.19
DIO15: JP142.2, U18.7
DIO16: JP143.3, U18.20
DIO17: JP143.2, U18.19
DIO18: JP166.2, U21.7
DIO19: JP167.3, U21.20
DIO20: JP167.2, U21.19
DIO21: JP190.2, U24.7
DIO22: JP191.3, U24.20
DIO23: JP191.2, U24.19
DOUT: D1.C, Q2.2, R12.1, U1.2
DOUT1: D18.C, Q8.2, R29.1, U6.2
DOUT2: D28.C, Q14.2, R47.1, U9.2
DOUT3: D38.C, Q20.2, R65.1, U12.2
DOUT4: D48.C, Q26.2, R83.1, U15.2
DOUT5: D58.C, Q32.2, R101.1, U18.2
DOUT6: D68.C, Q38.2, R119.1, U21.2
DOUT7: D78.C, Q44.2, R137.1, U24.2
FUSED_3.3V: F3.2, J2.2, Q1.1, Q2.1, R6.1, R7.1, R9.2, R11.2, R12.2, U1.1
FUSED_3.3V1: F5.2, J5.2, Q7.1, Q8.1, R24.1, R25.1, R27.2, R29.2, R31.2, U6.1
FUSED_3.3V2: F8.2, J8.2, Q13.1, Q14.1, R42.1, R43.1, R45.2, R47.2, R49.2, U9.1
FUSED_3.3V3: F11.2, J11.2, Q19.1, Q20.1, R60.1, R61.1, R63.2, R65.2, R67.2, U12.1
FUSED_3.3V4: F14.2, J14.2, Q25.1, Q26.1, R78.1, R79.1, R81.2, R83.2, R85.2, U15.1
FUSED_3.3V5: F17.2, J17.2, Q31.1, Q32.1, R96.1, R97.1, R99.2, R101.2, R103.2, U18.1
FUSED_3.3V6: F20.2, J20.2, Q37.1, Q38.1, R114.1, R115.1, R117.2, R119.2, R121.2, U21.1
FUSED_3.3V7: F23.2, J23.2, Q43.1, Q44.1, R132.1, R133.1, R135.2, R137.2, R139.2, U24.1
FUSED_5V: C2.1, F2.2, R10.2, R13.2, U3.19, U3.20
FUSED_5V1: C6.1, F1.2, R28.2, R30.2, U5.19, U5.20
FUSED_5V2: C10.1, F7.2, R46.2, R48.2, U8.19, U8.20
FUSED_5V3: C14.1, F10.2, R64.2, R66.2, U11.19, U11.20
FUSED_5V4: C18.1, F13.2, R82.2, R84.2, U14.19, U14.20
FUSED_5V5: C22.1, F16.2, R100.2, R102.2, U17.19, U17.20
FUSED_5V6: C26.1, F19.2, R118.2, R120.2, U20.19, U20.20
FUSED_5V7: C30.1, F22.2, R136.2, R138.2, U23.19, U23.20
FUSED_IOREF: F4.2, JP14.2, JP15.2, JP16.2, JP17.2, JP18.2, JP19.2, S1.2, S1.5
FUSED_IOREF1: F6.2, JP39.2, JP40.2, JP41.2, JP42.2, JP43.2, JP44.2, S7.2, S7.5
FUSED_IOREF2: F9.2, JP63.2, JP64.2, JP65.2, JP66.2, JP67.2, JP68.2, S11.2, S11.5
FUSED_IOREF3: F12.2, JP87.2, JP88.2, JP89.2, JP90.2, JP91.2, JP92.2, S15.2, S15.5
FUSED_IOREF4: F15.2, JP111.2, JP112.2, JP113.2, JP114.2, JP115.2, JP116.2, S19.2, S19.5
FUSED_IOREF5: F18.2, JP135.2, JP136.2, JP137.2, JP138.2, JP139.2, JP140.2, S23.2, S23.5
FUSED_IOREF6: F21.2, JP159.2, JP160.2, JP161.2, JP162.2, JP163.2, JP164.2, S27.2, S27.5
FUSED_IOREF7: F24.2, JP183.2, JP184.2, JP185.2, JP186.2, JP187.2, JP188.2, S31.2, S31.5
GND: C1.2, C2.2, C3.2, C4.2, D3.C, J1.GND, J2.1, J3.1, JP0.1, JP1.1, JP2.1, JP3.1, JP4.1, JP5.1, JP6.1, JP7.1, JP8.1, JP9.1, JP10.1, JP11.1, JP12.1, JP13.1, JP14.1, JP15.1, JP16.1, JP17.1, JP18.1, JP19.1, JP23.1, JP24.1, Q3.2, R5.1, R15.1, S3.2, S3.5, S4.1, S4.2, SJ5.2, TP9.P$1, U1.10, U2.GND@0, U2.GND@1, U2.GND@2, U3.3, U3.4, U3.9, U3.10, U3.18
GND1: C5.2, C6.2, C7.2, C8.2, D17.C, J4.GND, J5.1, J6.1, JP25.1, JP26.1, JP27.1, JP28.1, JP29.1, JP30.1, JP31.1, JP32.1, JP33.1, JP34.1, JP35.1, JP36.1, JP37.1, JP38.1, JP39.1, JP40.1, JP41.1, JP42.1, JP43.1, JP44.1, JP46.1, JP47.1, Q9.2, R23.1, R33.1, S5.1, S5.2, S8.2, S8.5, SJ1.2, TP21.P$1, U4.GND@0, U4.GND@1, U4.GND@2, U5.3, U5.4, U5.9, U5.10, U5.18, U6.10
GND2: C9.2, C10.2, C11.2, C12.2, D27.C, J7.GND, J8.1, J9.1, JP49.1, JP50.1, JP51.1, JP52.1, JP53.1, JP54.1, JP55.1, JP56.1, JP57.1, JP58.1, JP59.1, JP60.1, JP61.1, JP62.1, JP63.1, JP64.1, JP65.1, JP66.1, JP67.1, JP68.1, JP70.1, JP71.1, Q15.2, R41.1, R51.1, S9.1, S9.2, S12.2, S12.5, SJ2.2, TP33.P$1, U7.GND@0, U7.GND@1, U7.GND@2, U8.3, U8.4, U8.9, U8.10, U8.18, U9.10
GND3: C13.2, C14.2, C15.2, C16.2, D37.C, J10.GND, J11.1, J12.1, JP73.1, JP74.1, JP75.1, JP76.1, JP77.1, JP78.1, JP79.1, JP80.1, JP81.1, JP82.1, JP83.1, JP84.1, JP85.1, JP86.1, JP87.1, JP88.1, JP89.1, JP90.1, JP91.1, JP92.1, JP94.1, JP95.1, Q21.2, R59.1, R69.1, S13.1, S13.2, S16.2, S16.5, SJ3.2, TP45.P$1, U10.GND@0, U10.GND@1, U10.GND@2, U11.3, U11.4, U11.9, U11.10, U11.18, U12.10
GND4: C17.2, C18.2, C19.2, C20.2, D47.C, J13.GND, J14.1, J15.1, JP97.1, JP98.1, JP99.1, JP100.1, JP101.1, JP102.1, JP103.1, JP104.1, JP105.1, JP106.1, JP107.1, JP108.1, JP109.1, JP110.1, JP111.1, JP112.1, JP113.1, JP114.1, JP115.1, JP116.1, JP118.1, JP119.1, Q27.2, R77.1, R87.1, S17.1, S17.2, S20.2, S20.5, SJ4.2, TP57.P$1, U13.GND@0, U13.GND@1, U13.GND@2, U14.3, U14.4, U14.9, U14.10, U14.18, U15.10
GND5: C21.2, C22.2, C23.2, C24.2, D57.C, J16.GND, J17.1, J18.1, JP121.1, JP122.1, JP123.1, JP124.1, JP125.1, JP126.1, JP127.1, JP128.1, JP129.1, JP130.1, JP131.1, JP132.1, JP133.1, JP134.1, JP135.1, JP136.1, JP137.1, JP138.1, JP139.1, JP140.1, JP142.1, JP143.1, Q33.2, R95.1, R105.1, S21.1, S21.2, S24.2, S24.5, SJ6.2, TP69.P$1, U16.GND@0, U16.GND@1, U16.GND@2, U17.3, U17.4, U17.9, U17.10, U17.18, U18.10
GND6: C25.2, C26.2, C27.2, C28.2, D67.C, J19.GND, J20.1, J21.1, JP145.1, JP146.1, JP147.1, JP148.1, JP149.1, JP150.1, JP151.1, JP152.1, JP153.1, JP154.1, JP155.1, JP156.1, JP157.1, JP158.1, JP159.1, JP160.1, JP161.1, JP162.1, JP163.1, JP164.1, JP166.1, JP167.1, Q39.2, R113.1, R123.1, S25.1, S25.2, S28.2, S28.5, SJ7.2, TP81.P$1, U19.GND@0, U19.GND@1, U19.GND@2, U20.3, U20.4, U20.9, U20.10, U20.18, U21.10
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

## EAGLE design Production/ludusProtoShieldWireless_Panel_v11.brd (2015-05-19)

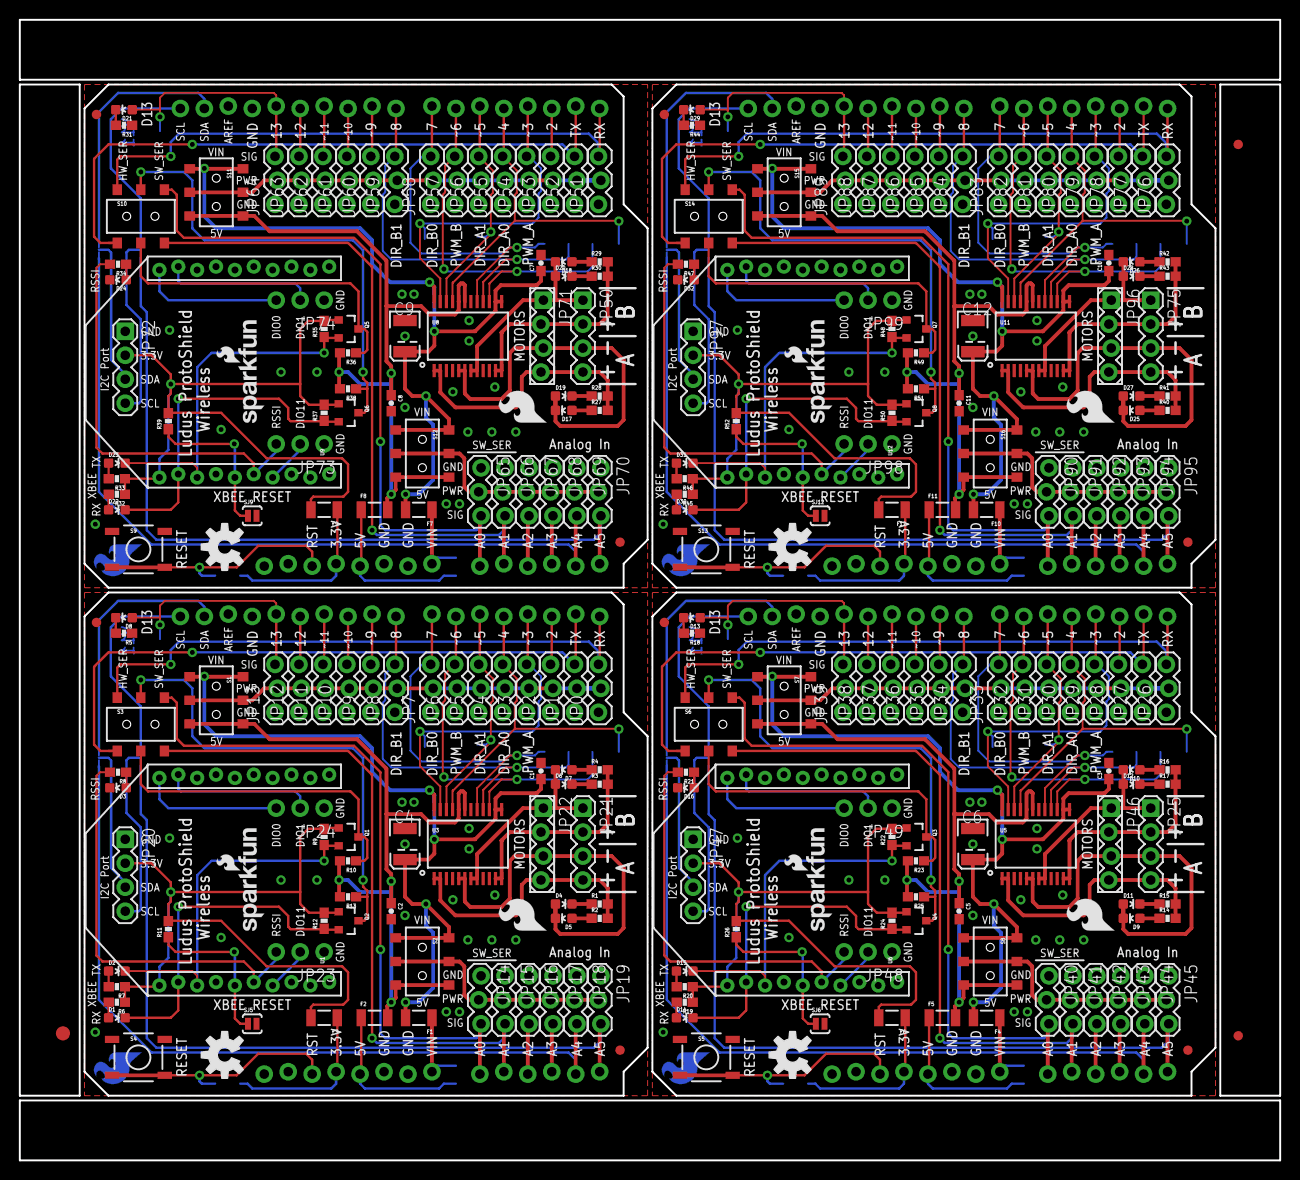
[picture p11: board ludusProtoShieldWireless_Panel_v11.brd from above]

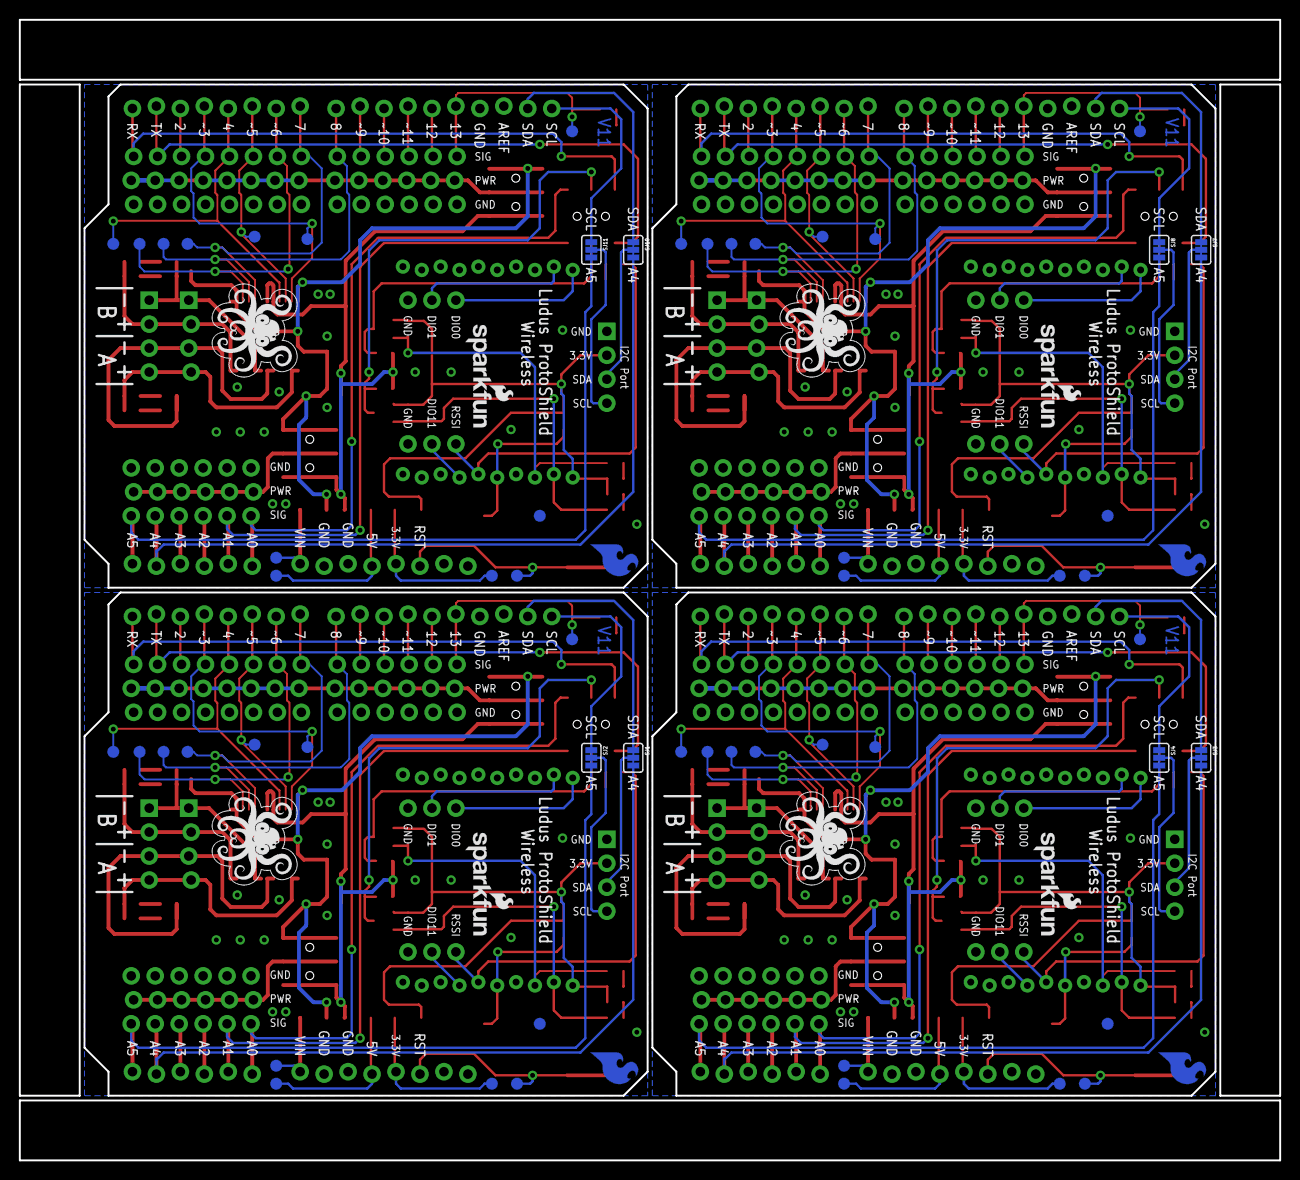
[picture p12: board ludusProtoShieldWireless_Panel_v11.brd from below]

Board: 2 copper layers, 133.6 x 120.9 mm, 339 parts (68 on the bottom side), 220 nets.

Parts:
C1, C2, C3, C5, C7, C8, C10, C11: 0.1uF; 0603-CAP
C4, C6, C9, C12: 10uf , 20V; EIA3528
D1, D14, D22, D30: Red; LED-0603
D2, D15, D23, D31: Green; LED-0603
D3, D5, D7, D9, D10, D16, D17, D18, D24, D25, D26, D32: Yellow; LED-0603
D4, D6, D8, D11, D12, D13, D19, D20, D21, D27, D28, D29: Blue; LED-0603
E$1: FIDUCIAL-1.5X3
E$4, E$5: FIDUCIAL-1X2
F1, F2, F3, F4, F5, F6, F7, F8, F9, F10, F11, F12: PTC-1206
FID1, FID2, FID3, FID4, FID5, FID6, FID7, FID8: FIDUCIAL1X2; FIDUCIAL-1X2
JP0, JP26, JP51, JP76: D0; 1X03_LOCK
JP1, JP27, JP52, JP77: D1; 1X03_LOCK
JP2, JP28, JP53, JP78: D2; 1X03_LOCK
JP3, JP29, JP54, JP79: D3; 1X03_LOCK
JP4, JP30, JP55, JP80: D4; 1X03_LOCK
JP5, JP31, JP56, JP81: D5; 1X03_LOCK
JP6, JP32, JP57, JP82: D6; 1X03_LOCK
JP7, JP33, JP58, JP83: D7; 1X03_LOCK
JP8, JP34, JP59, JP84: D8; 1X03_LOCK
JP9, JP35, JP60, JP85: D9; 1X03_LOCK
JP10, JP36, JP61, JP86: D10; 1X03_LOCK
JP11, JP37, JP62, JP87: D11; 1X03_LOCK
JP12, JP38, JP63, JP88: D12; 1X03_LOCK
JP13, JP39, JP64, JP89: D13; 1X03_LOCK
JP14, JP40, JP65, JP90: A0; 1X03_LOCK
JP15, JP41, JP66, JP91: A1; 1X03_LOCK
JP16, JP42, JP67, JP92: A2; 1X03_LOCK
JP17, JP43, JP68, JP93: A3; 1X03_LOCK
JP18, JP44, JP69, JP94: A4; 1X03_LOCK
JP19, JP45, JP70, JP95: A5; 1X03_LOCK
JP20, JP21, JP25, JP47, JP50, JP72, JP75, JP97: 1X04
JP22, JP46, JP71, JP96: 1X04_LOCK
JP23, JP24, JP48, JP49, JP73, JP74, JP98, JP99: 1X03_NO_SILK
LOGO1, LOGO6, LOGO11, LOGO16: OSHW-LOGOM; OSHW-LOGO-M
LOGO2, LOGO4, LOGO7, LOGO9, LOGO12, LOGO14, LOGO17, LOGO19: SFE_LOGO_NAME_FLAME.1_INCH; SFE_LOGO_NAME_FLAME_.1
LOGO3, LOGO8, LOGO13, LOGO18: SFE_LOGO_FLAME.2_INCH; SFE_LOGO_FLAME_.2
LOGO5, LOGO10, LOGO15, LOGO20: SFE_LOGO_FLAME.2COP; SFE_LOGO_FLAME_COPPER_.2
Q1, Q2, Q3, Q4, Q5, Q6, Q7, Q8: MOSFET-NCHANNELBSS138; SOT23-3
R1, R2, R3, R4, R6, R7, R8, R9, R10, R11, R12, R13, R14, R15, R16, R17, R19, R20, R21, R22, R23, R24, R25, R26, R27, R28, R29, R30, R32, R33, R34, R35, R36, R37, R38, R39, R40, R41, R42, R43, R45, R46, R47, R48, R49, R50, R51, R52: 1K; 0603-RES
R5, R18, R31, R44: 330; 0603-RES
S1, S2, S7, S8, S11, S12, S15, S16: AYZ0202
S3, S6, S10, S14: DPDT; AYZ0202
S4, S5, S9, S13: RESET; TACTILE-SWITCH-SMD
SJ1, SJ2, SJ3, SJ4, SJ7, SJ8, SJ10, SJ11: PAD-JUMPER-3-3OF3_NC_BY_TRACE_YES_SILK_FULL_BOX
SJ5, SJ6, SJ9, SJ12: SJ_2S-NO
TP1, TP2, TP3, TP4, TP5, TP6, TP7, TP8, TP9, TP10, TP11, TP12, TP13, TP14, TP15, TP16, TP17, TP18, TP19, TP20, TP21, TP22, TP23, TP24, TP25, TP26, TP27, TP28, TP29, TP30, TP31, TP32, TP33, TP34, TP35, TP36, TP37, TP38, TP39, TP40, TP41, TP42, TP43, TP44, TP45, TP46, TP47, TP48: PAD.03X.05
U1, U6, U9, U12: XBEE-1XBEE-1_LOCK; XBEE-1_LOCK
U2, U4, U7, U10: ARDUINO; UNO_R3_SHIELD_NOLABELS_LOCK
U3, U5, U8, U11: TB6612FNG; SSOP24
U$1, U$2, U$3, U$4: SFE_LUDUSSFE_LUDUS-M; SFE_LUDUS-M

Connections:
3.3V: F3.1, TP11.P$1, U2.3.3V
3.3V1: F6.1, TP23.P$1, U4.3.3V
3.3V2: F9.1, TP35.P$1, U7.3.3V
3.3V3: F12.1, TP47.P$1, U10.3.3V
5V: F2.1, TP8.P$1, U2.5V
5V1: F5.1, TP20.P$1, U4.5V
5V2: F8.1, TP32.P$1, U7.5V
5V3: F11.1, TP44.P$1, U10.5V
A0/SW_RXI: JP14.3, S3.3, U2.A0
A0/SW_RXI1: JP40.3, S6.3, U4.A0
A0/SW_RXI2: JP65.3, S10.3, U7.A0
A0/SW_RXI3: JP90.3, S14.3, U10.A0
A1: JP45.3, SJ2.3, U4.A5
A1/SW_TXO: JP15.3, S3.6, U2.A1
A1/SW_TXO1: JP41.3, S6.6, U4.A1
A1/SW_TXO2: JP66.3, S10.6, U7.A1
A1/SW_TXO3: JP91.3, S14.6, U10.A1
A2: JP16.3, U2.A2
A3: JP17.3, U2.A3
A4: JP18.3, SJ3.3, U2.A4
A5: JP19.3, SJ4.3, U2.A5
A6: JP44.3, SJ1.3, U4.A4
A7: JP42.3, U4.A2
A8: JP43.3, U4.A3
A9: JP70.3, SJ8.3, U7.A5
A10: JP69.3, SJ7.3, U7.A4
A11: JP67.3, U7.A2
A12: JP68.3, U7.A3
A13: JP95.3, SJ11.3, U10.A5
A14: JP94.3, SJ10.3, U10.A4
A15: JP92.3, U10.A2
A16: JP93.3, U10.A3
AIN1: JP4.3, TP1.P$1, U2.D4, U3.21
AIN2: JP5.3, TP2.P$1, U2.D5, U3.22
AIN3: JP31.3, TP14.P$1, U4.D5, U5.22
AIN4: JP30.3, TP13.P$1, U4.D4, U5.21
AIN5: JP56.3, TP26.P$1, U7.D5, U8.22
AIN6: JP55.3, TP25.P$1, U7.D4, U8.21
AIN7: JP81.3, TP38.P$1, U10.D5, U11.22
AIN8: JP80.3, TP37.P$1, U10.D4, U11.21
ANALOG_PWR_RAIL: JP14.2, JP15.2, JP16.2, JP17.2, JP18.2, JP19.2, S2.2, S2.5
ANALOG_PWR_RAIL1: JP40.2, JP41.2, JP42.2, JP43.2, JP44.2, JP45.2, S8.2, S8.5
ANALOG_PWR_RAIL2: JP65.2, JP66.2, JP67.2, JP68.2, JP69.2, JP70.2, S12.2, S12.5
ANALOG_PWR_RAIL3: JP90.2, JP91.2, JP92.2, JP93.2, JP94.2, JP95.2, S16.2, S16.5
AOUT1: JP21.4, JP22.4, R1.2, R2.2, U3.1, U3.2
AOUT2: D4.A, D5.C, JP21.3, JP22.3, U3.5, U3.6
AOUT3: JP25.4, JP46.4, R14.2, R15.2, U5.1, U5.2
AOUT4: D9.C, D11.A, JP25.3, JP46.3, U5.5, U5.6
AOUT5: JP50.4, JP71.4, R27.2, R28.2, U8.1, U8.2
AOUT6: D17.C, D19.A, JP50.3, JP71.3, U8.5, U8.6
AOUT7: JP75.4, JP96.4, R40.2, R41.2, U11.1, U11.2
AOUT8: D25.C, D27.A, JP75.3, JP96.3, U11.5, U11.6
BIN1: JP7.3, TP4.P$1, U2.D7, U3.17
BIN2: JP8.3, TP5.P$1, U2.D8, U3.16
BIN3: JP33.3, TP16.P$1, U4.D7, U5.17
BIN4: JP34.3, TP17.P$1, U4.D8, U5.16
BIN5: JP58.3, TP28.P$1, U7.D7, U8.17
BIN6: JP59.3, TP29.P$1, U7.D8, U8.16
BIN7: JP83.3, TP40.P$1, U10.D7, U11.17
BIN8: JP84.3, TP41.P$1, U10.D8, U11.16
BOUT1: JP21.2, JP22.2, R3.2, R4.2, U3.11, U3.12
BOUT2: D6.A, D7.C, JP21.1, JP22.1, U3.7, U3.8
BOUT3: D10.C, D12.A, JP25.1, JP46.1, U5.7, U5.8
BOUT4: JP25.2, JP46.2, R16.2, R17.2, U5.11, U5.12
BOUT5: D18.C, D20.A, JP50.1, JP71.1, U8.7, U8.8
BOUT6: JP50.2, JP71.2, R29.2, R30.2, U8.11, U8.12
BOUT7: D26.C, D28.A, JP75.1, JP96.1, U11.7, U11.8
BOUT8: JP75.2, JP96.2, R42.2, R43.2, U11.11, U11.12
D0/RXI: JP0.3, S3.1, U2.RX
D0/RXI1: JP26.3, S6.1, U4.RX
D0/RXI2: JP51.3, S10.1, U7.RX
D0/RXI3: JP76.3, S14.1, U10.RX
D1: JP38.3, U4.D12
D1/TXO: JP1.3, S3.4, U2.TX
D1/TXO1: JP27.3, S6.4, U4.TX
D1/TXO2: JP52.3, S10.4, U7.TX
D1/TXO3: JP77.3, S14.4, U10.TX
D2: JP2.3, U2.D2
D3: D13.A, JP39.3, TP19.P$1, U4.D13
D4: JP36.3, U4.D10
D5: JP28.3, U4.D2
D6: JP37.3, U4.D11
D7: JP35.3, U4.D9
D8: JP63.3, U7.D12
D9: JP9.3, U2.D9
D10: JP10.3, U2.D10
D11: JP11.3, U2.D11
D12: JP12.3, U2.D12
D13: D8.A, JP13.3, TP7.P$1, U2.D13
D14: D21.A, JP64.3, TP31.P$1, U7.D13
D15: JP61.3, U7.D10
D16: JP53.3, U7.D2
D17: JP62.3, U7.D11
D18: JP60.3, U7.D9
D19: JP88.3, U10.D12
D20: D29.A, JP89.3, TP43.P$1, U10.D13
D21: JP86.3, U10.D10
D22: JP78.3, U10.D2
D23: JP87.3, U10.D11
D24: JP85.3, U10.D9
DIN: D2.C, Q1.2, R9.1, U1.3
DIN1: D15.C, Q3.2, R22.1, U6.3
DIN2: D23.C, Q5.2, R35.1, U9.3
DIN3: D31.C, Q7.2, R48.1, U12.3
DIO0: JP24.3, U1.20
DIO1: JP24.2, U1.19
DIO2: JP48.2, U6.7
DIO3: JP49.3, U6.20
DIO4: JP49.2, U6.19
DIO5: JP73.2, U9.7
DIO6: JP74.3, U9.20
DIO7: JP74.2, U9.19
DIO8: JP98.2, U12.7
DIO9: JP99.3, U12.20
DIO10: JP99.2, U12.19
DIO11: JP23.2, U1.7
DOUT: D1.C, Q2.2, R12.1, U1.2
DOUT1: D14.C, Q4.2, R24.1, U6.2
DOUT2: D22.C, Q6.2, R37.1, U9.2
DOUT3: D30.C, Q8.2, R50.1, U12.2
FUSED_3.3V: F3.2, JP20.2, Q1.1, Q2.1, R6.1, R7.1, R9.2, R11.2, R12.2, U1.1
FUSED_3.3V1: F6.2, JP47.2, Q3.1, Q4.1, R19.1, R20.1, R22.2, R24.2, R26.2, U6.1
FUSED_3.3V2: F9.2, JP72.2, Q5.1, Q6.1, R32.1, R33.1, R35.2, R37.2, R39.2, U9.1
FUSED_3.3V3: F12.2, JP97.2, Q7.1, Q8.1, R45.1, R46.1, R48.2, R50.2, R52.2, U12.1
FUSED_5V: C2.1, F2.2, R10.2, R13.2, S1.3, S1.6, S2.3, S2.6, U3.19, U3.20
FUSED_5V1: C5.1, F5.2, R23.2, R25.2, S7.3, S7.6, S8.3, S8.6, U5.19, U5.20
FUSED_5V2: C8.1, F8.2, R36.2, R38.2, S11.3, S11.6, S12.3, S12.6, U8.19, U8.20
FUSED_5V3: C11.1, F11.2, R49.2, R51.2, S15.3, S15.6, S16.3, S16.6, U11.19, U11.20
FUSED_VIN: C1.1, C4.A, F1.2, S1.1, S1.4, S2.1, S2.4, U3.13, U3.14, U3.24
FUSED_VIN1: C3.1, C6.A, F4.2, S7.1, S7.4, S8.1, S8.4, U5.13, U5.14, U5.24
FUSED_VIN2: C7.1, C9.A, F7.2, S11.1, S11.4, S12.1, S12.4, U8.13, U8.14, U8.24
FUSED_VIN3: C10.1, C12.A, F10.2, S15.1, S15.4, S16.1, S16.4, U11.13, U11.14, U11.24
GND: C1.2, C2.2, C4.C, D3.C, JP0.1, JP1.1, JP2.1, JP3.1, JP4.1, JP5.1, JP6.1, JP7.1, JP8.1, JP9.1, JP10.1, JP11.1, JP12.1, JP13.1, JP14.1, JP15.1, JP16.1, JP17.1, JP18.1, JP19.1, JP20.1, JP23.1, JP24.1, R5.1, S4.1, S4.2, SJ5.2, TP9.P$1, U1.10, U2.GND@0, U2.GND@1, U2.GND@2, U3.3, U3.4, U3.9, U3.10, U3.18
GND1: C3.2, C5.2, C6.C, D16.C, JP26.1, JP27.1, JP28.1, JP29.1, JP30.1, JP31.1, JP32.1, JP33.1, JP34.1, JP35.1, JP36.1, JP37.1, JP38.1, JP39.1, JP40.1, JP41.1, JP42.1, JP43.1, JP44.1, JP45.1, JP47.1, JP48.1, JP49.1, R18.1, S5.1, S5.2, SJ6.2, TP21.P$1, U4.GND@0, U4.GND@1, U4.GND@2, U5.3, U5.4, U5.9, U5.10, U5.18, U6.10
GND2: C7.2, C8.2, C9.C, D24.C, JP51.1, JP52.1, JP53.1, JP54.1, JP55.1, JP56.1, JP57.1, JP58.1, JP59.1, JP60.1, JP61.1, JP62.1, JP63.1, JP64.1, JP65.1, JP66.1, JP67.1, JP68.1, JP69.1, JP70.1, JP72.1, JP73.1, JP74.1, R31.1, S9.1, S9.2, SJ9.2, TP33.P$1, U7.GND@0, U7.GND@1, U7.GND@2, U8.3, U8.4, U8.9, U8.10, U8.18, U9.10
GND3: C10.2, C11.2, C12.C, D32.C, JP76.1, JP77.1, JP78.1, JP79.1, JP80.1, JP81.1, JP82.1, JP83.1, JP84.1, JP85.1, JP86.1, JP87.1, JP88.1, JP89.1, JP90.1, JP91.1, JP92.1, JP93.1, JP94.1, JP95.1, JP97.1, JP98.1, JP99.1, R44.1, S13.1, S13.2, SJ12.2, TP45.P$1, U10.GND@0, U10.GND@1, U10.GND@2, U11.3, U11.4, U11.9, U11.10, U11.18, U12.10
unnamed: D8.C, R5.2
unnamed: D9.A, R14.1
unnamed: D5.A, R2.1
unnamed: D11.C, R15.1
unnamed: D4.C, R1.1
unnamed: D7.A, R4.1
unnamed: D6.C, R3.1
unnamed: D10.A, R16.1
unnamed: D12.C, R17.1
unnamed: D13.C, R18.2
unnamed: D14.A, R19.2
unnamed: D15.A, R20.2
unnamed: D16.A, R21.1
unnamed: D17.A, R27.1
unnamed: D19.C, R28.1
unnamed: D18.A, R29.1
unnamed: D20.C, R30.1
unnamed: D21.C, R31.2
unnamed: D22.A, R32.2
unnamed: D1.A, R6.2
unnamed: D23.A, R33.2
unnamed: D24.A, R34.1
unnamed: D25.A, R40.1
unnamed: D27.C, R41.1
unnamed: D26.A, R42.1
unnamed: D28.C, R43.1
unnamed: D29.C, R44.2
unnamed: D30.A, R45.2
unnamed: D31.A, R46.2
unnamed: D32.A, R47.1
unnamed: D2.A, R7.2
unnamed: D3.A, R8.1
PWMA: JP3.3, TP3.P$1, U2.D3, U3.23
PWMA1: JP29.3, TP15.P$1, U4.D3, U5.23
PWMA2: JP54.3, TP27.P$1, U7.D3, U8.23
PWMA3: JP79.3, TP39.P$1, U10.D3, U11.23
PWMB: JP6.3, TP6.P$1, U2.D6, U3.15
PWMB1: JP32.3, TP18.P$1, U4.D6, U5.15
PWMB2: JP57.3, TP30.P$1, U7.D6, U8.15
PWMB3: JP82.3, TP42.P$1, U10.D6, U11.15
PWR_RAIL: JP0.2, JP1.2, JP2.2, JP3.2, JP4.2, JP5.2, JP6.2, JP7.2, JP8.2, JP9.2, JP10.2, JP11.2, JP12.2, JP13.2, S1.2, S1.5
PWR_RAIL1: JP26.2, JP27.2, JP28.2, JP29.2, JP30.2, JP31.2, JP32.2, JP33.2, JP34.2, JP35.2, JP36.2, JP37.2, JP38.2, JP39.2, S7.2, S7.5
PWR_RAIL2: JP51.2, JP52.2, JP53.2, JP54.2, JP55.2, JP56.2, JP57.2, JP58.2, JP59.2, JP60.2, JP61.2, JP62.2, JP63.2, JP64.2, S11.2, S11.5
PWR_RAIL3: JP76.2, JP77.2, JP78.2, JP79.2, JP80.2, JP81.2, JP82.2, JP83.2, JP84.2, JP85.2, JP86.2, JP87.2, JP88.2, JP89.2, S15.2, S15.5
RESET: S4.3, S4.4, TP12.P$1, U2.RES
RESET1: S5.3, S5.4, TP24.P$1, U4.RES
RESET2: S9.3, S9.4, TP36.P$1, U7.RES
RESET3: S13.3, S13.4, TP48.P$1, U10.RES
RSSI: JP23.3, R8.2, U1.6
RSSI1: JP48.3, R21.2, U6.6
RSSI2: JP73.3, R34.2, U9.6
RSSI3: JP98.3, R47.2, U12.6
SCL: SJ4.1, U2.SCL
SCL1: SJ2.1, U4.SCL
SCL2: SJ8.1, U7.SCL
SCL3: SJ11.1, U10.SCL
SCL_I2C_PORT: JP20.4, SJ4.2
SCL_I2C_PORT1: JP47.4, SJ2.2
SCL_I2C_PORT2: JP72.4, SJ8.2
SCL_I2C_PORT3: JP97.4, SJ11.2
SDA: SJ3.1, U2.SDA
SDA1: SJ1.1, U4.SDA
SDA2: SJ7.1, U7.SDA
SDA3: SJ10.1, U10.SDA
SDA_I2C_PORT: JP20.3, SJ3.2
SDA_I2C_PORT1: JP47.3, SJ1.2
SDA_I2C_PORT2: JP72.3, SJ7.2
SDA_I2C_PORT3: JP97.3, SJ10.2
VIN: F1.1, TP10.P$1, U2.VIN
VIN1: F4.1, TP22.P$1, U4.VIN
VIN2: F7.1, TP34.P$1, U7.VIN
VIN3: F10.1, TP46.P$1, U10.VIN
XBEE_RESET: R11.1, SJ5.1, U1.5
XBEE_RESET1: R26.1, SJ6.1, U6.5
XBEE_RESET2: R39.1, SJ9.1, U9.5
XBEE_RESET3: R52.1, SJ12.1, U12.5
XBEE_RXI: Q2.3, R13.1, S3.2
XBEE_RXI1: Q4.3, R25.1, S6.2
XBEE_RXI2: Q6.3, R38.1, S10.2
XBEE_RXI3: Q8.3, R51.1, S14.2
XBEE_TXO: Q1.3, R10.1, S3.5
XBEE_TXO1: Q3.3, R23.1, S6.5
XBEE_TXO2: Q5.3, R36.1, S10.5
XBEE_TXO3: Q7.3, R49.1, S14.5

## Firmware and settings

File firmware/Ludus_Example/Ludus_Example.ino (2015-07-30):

/*
 * SparkFun Ludus ProtoShield Example Code
 * SparkFun Electronics
 * Nick Poole 2015
 * 
 * This is an Arduino shield that integrates an H-Bridge Driver and 
 * breaks out all I/O ports to three-pin headers on a GND/PWR/SIG 
 * standard. This enables quick prototyping and integration of 
 * Arduino projects w/o the need of a breadboard.
 * 
 * Ludus is the mascot of the SparkFun Education team. 
 * It is a highly intelligent octopus.
 * 
 * Please see the License.md file for license information.
*/

#include <Servo.h> 

Servo swivel;

int pwm_a = 3;   // Channel A speed
int pwm_b = 6;   // Channel B speed
int dir_a0 = 4;  // Channel A direction 0
int dir_a1 = 5;  // Channel A direction 1
int dir_b0 = 7;  // Channel B direction 0
int dir_b1 = 8;  // Channel B direction 1

char inbit; // A place to store serial input

int swivelpos = 90; // Servo position

void setup()
{

  Serial.begin(9600); // Pour a bowl of serial

  swivel.attach(11); // Attach servo to pin 11
  swivel.write(swivelpos); 
  
  pinMode(pwm_a, OUTPUT);  // Set control pins to be outputs
  pinMode(pwm_b, OUTPUT);
  pinMode(dir_a0, OUTPUT);
  pinMode(dir_a1, OUTPUT);
  pinMode(dir_b0, OUTPUT);
  pinMode(dir_b1, OUTPUT);

  draw(); // Draw the driving instructions to the serial terminal
  
}

void loop()
{ 

if(Serial.available()){ // Wait for serial input

  inbit = Serial.read();
 
  switch(inbit){ // Switch based on serial in

    case 'w': // Move Forward

      forward(200);
      delay(30);
      shutoff();
      break;

    case 's': // Move Backward

      reverse(200);
      delay(30);
      shutoff();
      break;

    case 'q': // Turn Left while moving forward

      turnL(200);
      delay(30);
      shutoff();
      break;
        
    case 'e': // Turn Right while moving forward

      turnR(200);
      delay(30);
      shutoff();
      break;

    case 'a': // Spin Left in place

      spinL(200);
      delay(30);
      shutoff();
      break;
  
    case 'd': // Spin Right in place

      spinR(200);
      delay(30);
      shutoff();
      break;

    case 'x': // Short brake

      brake();
      break;

    case 'z': // Spin servo (on pin 11) left

      servoL();
      break;

    case 'c': // Spin servo (on pin 11) right

      servoR();
      break;

    }
  }  
}

void forward(int speed) // Move Forward
{ 

digitalWrite(dir_a0, 0);
digitalWrite(dir_a1, 1);
digitalWrite(dir_b0, 0);
digitalWrite(dir_b1, 1);

analogWrite(pwm_a, speed); 
analogWrite(pwm_b, speed); 

}

void reverse(int speed) // Move Backward 
{

digitalWrite(dir_a0, 1);
digitalWrite(dir_a1, 0);
digitalWrite(dir_b0, 1);
digitalWrite(dir_b1, 0);

analogWrite(pwm_a, speed); 
analogWrite(pwm_b, speed); 
 
}

void turnL(int speed) // Turn Left while moving forward
{ 

digitalWrite(dir_a0, 0);
digitalWrite(dir_a1, 1);
digitalWrite(dir_b0, 0);
digitalWrite(dir_b1, 1);

analogWrite(pwm_a, speed); 
analogWrite(pwm_b, speed/4); 

}

void turnR(int speed) // Turn Right while moving forward
{ 

digitalWrite(dir_a0, 0);
digitalWrite(dir_a1, 1);
digitalWrite(dir_b0, 0);
digitalWrite(dir_b1, 1);

analogWrite(pwm_a, speed/4); 
analogWrite(pwm_b, speed); 

}


void spinL(int speed) // Spin Left in place
{ 

digitalWrite(dir_a0, 0);
digitalWrite(dir_a1, 1);
digitalWrite(dir_b0, 1);
digitalWrite(dir_b1, 0);

analogWrite(pwm_a, speed/2); 
analogWrite(pwm_b, speed/2); 

}

void spinR(int speed) // Spin Right in place
{ 

digitalWrite(dir_a0, 1);
digitalWrite(dir_a1, 0);
digitalWrite(dir_b0, 0);
digitalWrite(dir_b1, 1);

analogWrite(pwm_a, speed/2); 
analogWrite(pwm_b, speed/2); 

}

void brake() // Short brake
{ 

digitalWrite(dir_a0, 1);
digitalWrite(dir_a1, 1);
digitalWrite(dir_b0, 1);
digitalWrite(dir_b1, 1);

analogWrite(pwm_a, 0); 
analogWrite(pwm_b, 0);

}

void shutoff() // Stop Motors w/o braking
{ 

digitalWrite(dir_a0, 0);
digitalWrite(dir_a1, 0);
digitalWrite(dir_b0, 0);
digitalWrite(dir_b1, 0);

analogWrite(pwm_a, 0); 
analogWrite(pwm_b, 0);

}

void draw() // Serial Instructions
{
  Serial.println("          DuckBot 2015          ");
  Serial.println("                                ");
  Serial.println("   -------------------------    ");
  Serial.println("   |       |       |       |    ");
  Serial.println("   |   Q   |   W   |   E   |    ");
  Serial.println("   | turnL |forward| turnR |    ");
  Serial.println("   -------------------------    ");
  Serial.println("   |       |       |       |    ");
  Serial.println("   |   A   |   S   |   D   |    ");
  Serial.println("   | spinL |reverse| spinR |    ");
  Serial.println("   -------------------------    ");
  Serial.println("   |       |       |       |    ");
  Serial.println("   |   Z   |   X   |   C   |    ");
  Serial.println("   |servo L| brake |servo R|    ");
  Serial.println("   -------------------------    ");
  Serial.println("                                ");
}

void servoL() // Spin servo (on pin 11) left 
{

  if(swivelpos>10){
    swivelpos = swivelpos-10;
    swivel.write(swivelpos);
  }

}

void servoR() // Spin servo (on pin 11) right
{
  
  if(swivelpos<170){
    swivelpos = swivelpos+10;
    swivel.write(swivelpos);
  }

}

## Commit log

2014-08-18 Initial Commit
    Initial board files
    [ProtoCAT.brd, ProtoCAT.sch]
2014-08-18 Updates per - engineering review mtg 8/18
    added prototyping area
    added cut/solder jumpers for A4/A5 SDA/SCL lines for Leo
    added ~PWM labels on pins 3, 5, 6, 9, 10, 11
    [ProtoCAT.brd, ProtoCAT.sch]
2014-08-19 Updated a few aesthetic elements on bottom side
    Included Ludus and sparkfun logo on bottom layer
    [ProtoCAT.brd, ProtoCAT.sch]
2014-09-03 Updated fuse to 1206 part on Vcc Line
    [ProtoCAT.brd, ProtoCAT.csv, ProtoCAT.sch]
2014-10-03 Removed unused layers
    Removed unused layers and backup b# / s# files
    [ProtoCAT.brd, ProtoCAT.sch]
2014-10-16 Moved 4 pin SMD headers to Motor Driver
    Tied STDBY pin on motor driver to Vcc, added 4 pin SMD header to motor
    Driver output, and changed 3-pin headers to locking headers
    [ProtoCAT.brd, ProtoCAT.sch]
2014-10-16 Removed unused layers on board
    Removed unused middle layers of board and cleaned up silkscreen artwork
    on Ludus Logo
    [ProtoCAT.brd]
2014-10-28 Final board changes -- ready for reds
    Moved I2C header down to account for panelizer, moved a the cut jumpers
    for A4/A5 & SCL/SDA on bottom trace
    [ProtoCAT.brd]
2014-10-28 Updated version to v10
    Final updates with silk changes, version number, and repo clean-up.
    [ProtoCAT.brd, ProtoCAT.csv]
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2014-11-18 Initial Commit
    Updated / Changed ProtoCAT to include an XBee header
    [ProtoCAT.brd, ProtoCAT.sch]
2014-12-05 Updated XBee footprint and added RESET control
    Added RESET for XBee and fixed PWR lines to the XBee
    [ProtoCAT_wireless.brd, ProtoCAT_wireless.sch]
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2014-12-09 clean-up - removed excess files
    removed extra board files and production panel
    [ProtoCAT-Panel-v10.brd]
2015-01-08 Switched TX / RX lines on XBee
    Fixed the Switched TX / RX lines from XBee to Arduino on the HW Serial
    lines.
    Moved the thru-hole mounts for the Motors to below the SMD mount.
    Fixed LEDs for RSSI, DIN / DOUT
    [ProtoCAT_wireless.brd, ProtoCAT_wireless.csv, ProtoCAT_wireless.sch]
2015-01-08 Changed the Silkscreen name to Ludus Wireless Shield
    [ProtoCAT_wireless.brd]
2015-01-08 Added break-out for 4 I/O pins on XBee
    Added breakout pins for DIO0, DIO1, P0, P1 and GND to the board.
    [ProtoCAT_wireless.brd, ProtoCAT_wireless.sch]
2015-01-09 Updated Silk
    Added additional silk to show the SW Serial connection on the shield
    [ProtoCAT_wireless.brd]
2015-01-15 Updated shield footprint to include staggered / locking holes
    * changed filenames to ludusProtoShieldWireless
    * repo name will change after this commit
    [ProtoCAT_wireless.csv, ludusProtoShieldWireless.brd, ludusProtoShieldWireless.sch]
2015-02-09 Updated to fix all issues -
    Also added a switch to shield for switching between VIN and 5V
    [ludusProtoShieldWireless.brd, ludusProtoShieldWireless.sch]
2015-02-10 Approved all errors / warnings on ERC
    [ludusProtoShieldWireless.brd, ludusProtoShieldWireless.sch]
2015-02-10 Updated all issues in SCH.
    Also, replaced the switch for the DPDT package.
    [ludusProtoShieldWireless.brd, ludusProtoShieldWireless.sch]
2015-02-10 Fixed 2 GND flags and SJ5
    Updated nets on SJ5 and GND flags
    [ludusProtoShieldWireless.brd, ludusProtoShieldWireless.sch]
2015-02-10 Updating board to include measures and line up silk
    Updating board file
    [ludusProtoShieldWireless.brd]
2015-02-10 Spaced out LEDs / Resistors
    Fixed D1 / DOUT break and spaced out LEDs from resistors
    [ludusProtoShieldWireless.brd, ludusProtoShieldWireless.sch]
2015-02-11 Airwire on R7 fixed.
    [ludusProtoShieldWireless.brd]
2015-03-02 Minor Silk changes
    Changed the silk on the I2C port so that a rt angle connector does not
    block the pin descriptors.
    Also changed the DIN / DOUT text on the XBee to RX / TX respectively
    from the radio's point of view.
    [ludusProtoShieldWireless.brd, ludusProtoShieldWireless.sch]
2015-03-02 Added labels to bSilk layer
    Added pin labels to bSilk
    [ludusProtoShieldWireless.brd, ludusProtoShieldWireless.sch]
2015-03-05 Updates to final v1.0
    Ready for reds. Reviewed by Engineering.
    [ludusProtoShieldWireless.brd, ludusProtoShieldWireless.sch]
2015-03-30 Updated for QC issues for Reds
    [ludusProtoShieldWireless.brd, ludusProtoShieldWireless.sch]
2015-03-30 Moved test points around away from selective soldering points
    Moved testpoints around away from selective soldering points.
    [ludusProtoShieldWireless.brd]
2015-03-31 Updated silk images
    Updated all silk images using Pete's new artwork. Bumped test point away
    from header field
    [ludusProtoShieldWireless.brd]
2015-04-13 Moved PWM pins to 3 and 6 instead of 6 and 9
    Changed the PWM control pins on the shield to pins 3 & 6 so that it is
    compatible / does not conflict with the Arduino Servo library.
    No test points moved. Updated silk accordingly.
    [ludusProtoShieldWireless.brd, ludusProtoShieldWireless.sch]
2015-04-13 Updated version to 1.1
    [ludusProtoShieldWireless.brd]
2015-04-14 Updates re: Issue #4
    Fixed labels on LED7 to D1.
    Bumped the HW /SW Serial switch over to avoid the silk
    [ludusProtoShieldWireless.brd, ludusProtoShieldWireless.sch]
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2015-07-30 Updating README, adding LICENSE.md file
    [ludusProtoShieldWireless_Panel_v11.brd]
2017-04-26 Made changes for v12 protos
    [Wireless_Motor_Driver_Shield.brd, Wireless_Motor_Driver_Shield.sch]
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2017-05-02 Added new monster voltage select circuit to servo power rail
    [Wireless_Motor_Driver_Shield.brd, Wireless_Motor_Driver_Shield.sch]
2017-05-02 Added fiducials, cleaned up silk, added staking vias
    [Wireless_Motor_Driver_Shield.brd, Wireless_Motor_Driver_Shield.sch]
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2017-05-31 Added female I2C header. Added manual selector switch for VIN/VS with new barrel jack to power motors separately.
    [Wireless_Motor_Driver_Shield.brd, Wireless_Motor_Driver_Shield.sch]
2017-06-01 Added staking vias to barrel jack. Added header PTH for VS.
    [Wireless_Motor_Driver_Shield.brd, Wireless_Motor_Driver_Shield.sch]
2017-06-02 Moved silkscreen board name up a skosh to avoid via.
    [Wireless_Motor_Driver_Shield.brd]
2017-06-19 Changed to v14. Changed switch labels to VMOTOR
    [Wireless_Motor_Driver_Shield.brd, Wireless_Motor_Driver_Shield.sch]
2017-06-20 Changed switches silk and added arrows in silk to show what switches do
    [Wireless_Motor_Driver_Shield.brd]
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2017-06-23 Updated LED, RES, and CAP libraries to remove silk under parts
    [Wireless_Motor_Driver_Shield.brd, Wireless_Motor_Driver_Shield.sch]

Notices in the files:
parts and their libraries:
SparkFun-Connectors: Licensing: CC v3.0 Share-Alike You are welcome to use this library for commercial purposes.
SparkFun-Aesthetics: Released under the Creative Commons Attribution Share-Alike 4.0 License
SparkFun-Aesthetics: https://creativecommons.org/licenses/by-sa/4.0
